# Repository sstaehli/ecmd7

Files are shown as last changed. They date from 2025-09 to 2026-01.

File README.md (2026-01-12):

# ECMD7

3-Phase Power Converter Hardware for Motor Drive Experiments.

Check the [documentation pages on gitlab.airhead.ch](https://gitlab-pages.airhead.ch/products/arnimatic/ecmd7/) or [documentation pages on GitHub](https://sstaehli.github.io/ecmd7/) for more info.

[](
https://github.com/sstaehli/ecmd7/actions/workflows/ci.yml
)

[](
https://gitlab.airhead.ch/products/arnimatic/ecmd7/-/pipelines
)

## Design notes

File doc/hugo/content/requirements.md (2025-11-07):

---
title: "Requirements"
---

# User Requirements

## 1. Overview

The drive card should provide a power stage with high qualitiy features to drive a 3-phase motor from typical car lead or RC style lithium batteries for educational and development purposes. The PCB shall provide the required frontend to an external controller at a common logic level.
The design shall be cost optimized where possible without compromising functionality under lab conditions. The PCB shall interface directly with common low to mid priced FPGA development boards and should be easily adaptible to interface with other boards. The PCB shall provide sufficent power supply to the connected controller for standalone, mobile operation.

- Drive **500W** PMSM and other synchronous **motors** from 12V–48V (lead-acid or lithium)
- Based on **TMC6200 gate driver**
- All phase current & bus voltage **sensing** in high resolution (>12-Bit, $f_s >= 2f_{PWM}$)
- Multiple **encoder** support (ABZ, BISS-C/SSI, optionally SPI)
- Interfaces with **Arty A7**, **Zybo Z7**, or optionally **Vidor 4000**

---
## 2. Power Stage

The design shall be dimensioned for high currents to continuously deliver up to 500W from down to 12V upt to 60V. PWM frequencies shall be supported at least from 4 kHz up to 25kHz. 4 quadrant operation shall be possible with battery, an onboard or external brake chopper is optional.

- **Input Voltage**: 12V–48V (up to 60V abs max)
- **Output**: 35A RMS, 50A peak
- **External MOSFETs** (N-channel, low R_DS(on))
- **Bulk capacitors** for ripple suppression
- Reverse polarity & overvoltage protection

---
## 3. Gate Driver: TMC6200

The TCM6200 shall be chosen due to its specs matching or exceeding the requiremnts of the power stage and support for current sensing.

- 3-phase gate driver with:
  - 3x or 6x PWM support
  - SPI config & diagnostics
  - Shoot-through & UV/OV protection
  - Charge pump for 100% duty cycle
- Interfaces directly with external MOSFETs
- Supports external current sensing

---
## 4. Sensing

The design shall enable PWM synchronous sampling of all three phase currents and the DC bus voltage.

- **Current**: 3-phase sensing (inline or low-side), routed to FPGA
- **Voltage**: Phase voltages + DC bus
- **Temperature**: Optional NTC or digital sensor input for MOSFET temp

---
## 5. Encoder Interface

The design shall provide at least one commonly used sensor interface.

- Supports:
  - **BiSS-C**, **SSI**
  - **ABZ incremental**
  - **SPI encoders** (e.g., AS5047)
- 12V/5V/3.3V switchable encoder supply
- Up to 12V tolerant inputs
- ESD protection & differential receivers

---
## 6. FPGA / Logic Interface

The design shall mechanically fit directly to Digilent Arty A7 or Zybo Z7 development board.

- **PMOD-compatible** I/O headers (3.3V)
- FPGA interfaces:
  - PWM (3 or 6)
  - SPI (TMC6200, encoders)
  - Encoder signals (ABZ, BiSS-C, etc.)
- Compatible with:
  - **Arty A7**
  - **Zybo Z7**
  - **Intel Vidor 4000** (via adapter)

---
## 7. Mechanical

- PCB Size: ≤ 150mm x 100mm
- Mounting holes for heatsink/enclosure
- Connectors:
  - XT60 or screw terminals (power)
  - Screw terminals for motor phases
  - Pin headers for logic & encoders

---
## 8. Deliverables
- KiCad schematic + PCB layout
- BOM

---
## Example System Overview

```mermaid
graph TD
subgraph Power Stage
Q[Gate Driver]
W[VBus ADC]
E[U/V/W Current ADC]
R[Sensor Interface]
T[3-Phase Bridge]
Q --> T
T -.-> E
end
subgraph Dev. Kit
A[PMOD X]
B[PMOD Y]
C[PMOD Z]
end
A --> Q
W --> B
E --> B
T --> M(Motor)
M -.-> X(Sensor)
X --> R
R --> C
P(Battery) --> W
P --> T
```

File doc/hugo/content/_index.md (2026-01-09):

---
title: "Overview"
---

This is the ECMD7 reference manual. The ECMD7 - Electronically Controlled Motor Driver - is a 500W, three-phase bridge for supply voltages from 10 to 60V.

Check sources on [gitlab.airhead.ch](https://gitlab.airhead.ch/products/arnimatic/ecmd7) or [GitHub](https://github.com/sstaehli/ecmd7) 

ECMD7 PCB

The drive card provides a power stage with high qualitiy features to drive a 3-phase motor from typical car lead or RC style lithium batteries for educational and development purposes. The PCB provides the required frontend to an external controller at a common logic level.
The design is cost optimized where possible without compromising functionality under lab conditions. It can directly interface  with Digilent Arty A7 and Digilent Zybo Z7. Due to 2.54 pin headers it is easily adaptible to interface with other boards. The PCB can provide sufficent power supply to the connected controller for standalone, mobile operation.

- Drive **500W** PMSM and other synchronous **motors** from 12V–48V (lead-acid or lithium)
- Based on **TMC6200 gate driver**
- All phase current & bus voltage **sensing** in high resolution (14-Bit, $f_s>=2f_{PWM}$)
- Multiple **encoder** support (ABZ, BISS-C/SSI)
- Interfaces with **Arty A7**, **Zybo Z7**

### Additional Features

- **Onboard 12V/3A supply** for connected controller boards
- **Onboard 5V/2.5A supply** for connecting controller boards
- Dedicated **SPI diagnostic bus** with 2-to-4-line decoded chip select for:
    - TMC6200 gate driver
    - MB85RS* FRAM with at least 64kByte
    - TPM122 temperature sensor close to gate driver and power stage
- **Onboard LED** for supply rails
- **Onboard LED** for drive control and state signals
- **Probe test points** for measurments
- **Assembly options** for single ended or open collector encoder inputs to acommodate single ended encoders or hall switches
- **Selectable sensor supply**
- **Selectable 3.3V I/O voltage** internal or external

ECMD7 PCB

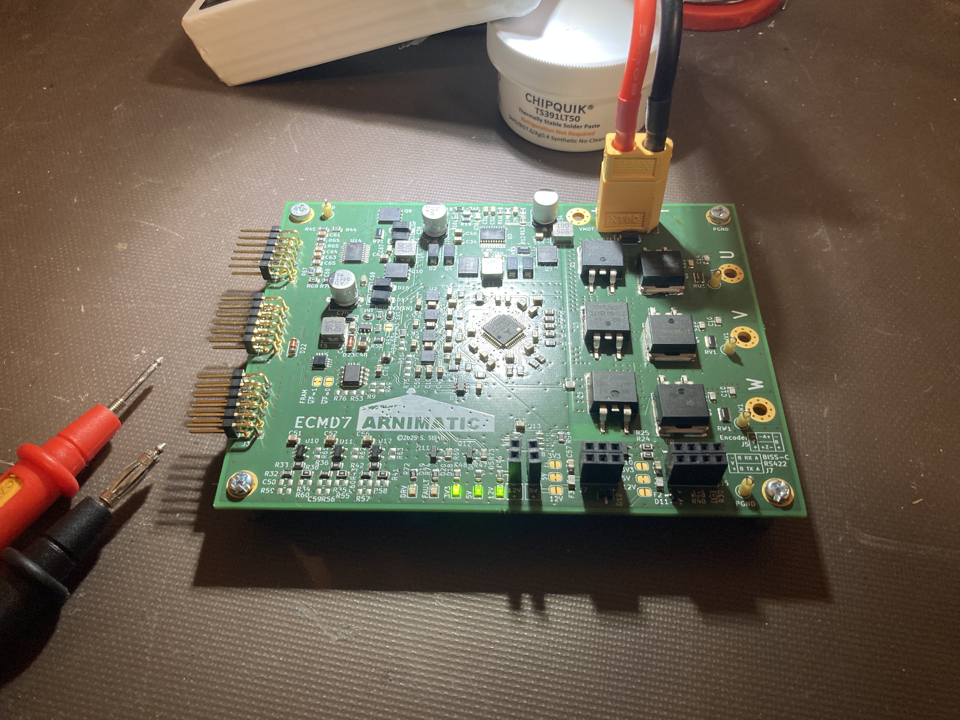
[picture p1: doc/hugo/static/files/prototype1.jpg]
ECMD7 First Prototype


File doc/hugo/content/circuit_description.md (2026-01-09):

---
title: "Circuit Description"
weight: 10
---

## Overview And PMOD Control Interface

The design mechanically fits the Digilent Arty A7 or Zybo Z7 development board.

- **PMOD-compatible** I/O headers (3.3V)
- FPGA interfaces:
  - PWM (3+3 driver signals)
  - SPI (TMC6200, encoders)
  - Encoder signals (ABZ, BiSS-C)
  - Compatible with:
    - **Arty A7**
    - **Zybo Z7**

### PMOD SPI & Encoder (J1)

| Pin # | Signal | I/O | PMOD JB (A7)*, PMOD JC (Z7)** | A7 FPGA Pin #* | Z7 SoC Pin #** | Description |
| - | - | - | - | - | - | - |
| 1 | 3.3V | In | 6 | - | - | I/O supply from FPGA board |
| 2 | 3.3V | In | 12 | - | - | I/O supply from FPGA board |
| 3 | GND | In | 5 | - | - | Signal GND |
| 4 | GND | In | 11 | - | - | Signal GND |
| 5 | ENC_B | Out | 4 | C15 | T10 | Quadrature encoder B signal |
| 6 | ENC_A | Out | 10 | J15 | U12 | Quadrature encoder A signal |
| 7 | CS1 | In | 3 | D15 | T11 | SPI Chip delect 1 for 2-to-4-line decoder |
| 8 | ENC_Z | Out | 9 | K15 | T12 | Quadrature encoder Z (Ref) signal |
| 9 | SPI_SCK | In | 2 | E16 | W15 | SPI Clock |
| 10 | CS0 | In | 8 | J18 | Y14 | SPI Chip delect 0 for 2-to-4-line decoder |
| 11 | SPI_SDI | In | 1 | E15 | V15 | SPI serial data in (from Controller) |
| 12 | SPI_SDO | Out/HiZ | 7 | J17 | W14 | SPI serial data out (to controller) |

### PMOD ADC & BiSS-C/RS422 Rx/Tx (J2)

| Pin # | Signal | I/O | PMOD JC (A7)*, PMOD JD (Z7)** | A7 FPGA Pin #* | Z7 SoC Pin #** | Description |
| - | - | - | - | - | - | - |
| 1 | 3.3V | In | 6 | - | - | I/O supply from FPGA board |
| 2 | 3.3V | In | 12 | - | - | I/O supply from FPGA board |
| 3 | GND | In | 5 | - | - | Signal GND |
| 4 | GND | In | 11 | - | - | Signal GND |
| 5 | RS422_RX | Out | 4 | V11 | R14 | RS422 receive signal (to controller) |
| 6 | RS422_TX | In | 10 | U13 | V18 | RS422 transmit signal (from controller) |
| 7 | AD_SDO_IW | Out | 3 | V10 | P14 | SPI serial data output from W-Phase current ADC |
| 8 | AD_SDO_VBUS | Out | 9 | T13 | V17 | SPI serial data output from bus voltage ADC |
| 9 | AD_SDO_IU | Out | 2 | V12 | T15 | SPI serial data output from U-Phase current ADC |
| 10 | AD_SDO_IV | Out | 8 | V14 | U15 | SPI serial data output from V-Phase current ADC |
| 11 | /CS_AD | In | 1 | U12 | T14 | SPI /CS line. Rising edge starts conversion, low level enables data output on AD_SCK rising edges |
| 12 | AD_SCK | In | 7 | U14 | W14 | SPI clock signal |

### PMOD Drive Control (J3)

| Pin # | Signal | I/O | PMOD JD (A7)*, PMOD JE (Z7)** | A7 FPGA Pin #* | Z7 SoC Pin #** | Description |
| - | - | - | - | - | - | - |
| 1 | 3.3V | In | 6 | - | - | I/O supply from FPGA board |
| 2 | 3.3V | In | 12 | - | - | I/O supply from FPGA board |
| 3 | GND | In | 5 | - | - | Signal GND |
| 4 | GND | In | 11 | - | - | Signal GND |
| 5 | DRV_EN | Out | 4 | F3 | H15 | Gate driver enable signal, active high |
| 6 | FAULT | In | 10 | G2 | Y17 | Gate driver fault signal, active high |
| 7 | WL | Out | 3 | F4 | J15 | Phase W low side switch control |
| 8 | WH | Out | 9 | H2 | T17 | Phase W high side switch control |
| 9 | VL | Out | 2 | D3 | W16 | Phase V low side switch control |
| 10 | VH | Out | 8 | D2 | U17 | Phase V high side switch control |
| 11 | UL | Out | 1 | D4 | V12 | Phase U low side switch control |
| 12 | UH | Out | 7 | E2 | V13 | Phase U high side switch control |

#### References

> *[Digilent Arty A7 Reference Manual](https://digilent.com/reference/programmable-logic/arty-a7/reference-manual)

> **[Digilent Zybo Z7 Reference Manual](https://digilent.com/reference/programmable-logic/zybo-z7/reference-manual)

---
## Power Stage

The design is dimensioned for high currents to continuously deliver up to 500W from 12V up to 60V. PWM frequencies are supported from 4 kHz up to 25kHz. 4 quadrant operation is possible with battery. There is no brake chopper.

- **Input Voltage**: 12V–48V (up to 60V abs max)
- **Output**: 35A RMS, 50A peak
- **60V/40A, low RDSOn MOSFETs** (N-channel, low R_DS(on))
- Mechanical reverse polarity protection
- Overvoltage protection

### Battery (J4) and Motor Phase Connections (U, V, W)

- A 12-48 Battery or 4-Qudrant Power Supply can be connected to the **XT60 connector J4** or the mounting holes **PGND** and **VMot**
- The Motor terminals can be connected to **M3 mounting holes U, V and W**

### Gate Driver (U1)

The [TCM6200](../files/datasheet/TMC6200_datasheet_rev1.08.pdf) matches or exceeds the requiremnts for controlling the power stage and provides support for current sensing.

- 3-phase gate driver with:
  - 3x or 6x PWM support
  - SPI config & diagnostics
  - Shoot-through & UV/OV protection
  - Charge pump for 100% duty cycle
- Interfaces directly with external MOSFETs
- Supports external current sensing

---
## ADC

The design supports PWM synchronous sampling of all three phase currents and the DC bus voltage.

- **Current**: 3-phase sensing (inline or low-side), routed to FPGA
- **Voltage**: Phase voltages + DC bus
- **Temperature**: digital sensor input for MOSFET temp

The ADC are of type [MCP3315141](../files/datasheet/MCP3315141-Data-Sheet-DS20006220.pdf)

---
## Sensors

The design provides two commonly used sensor interfaces.

- Supports:
  - **ABZ incremental**
  - **BiSS-C**, **SSI**
- 12V/5V/3.3V switchable encoder supply
- Up to 12V tolerant inputs
- differential receivers for ABZ incremental encorer
- RS422 Rx/Tx for BiSS-C
- ESD protection on all inputs

The quadrature encoder interface transforms differential signals to single ended 3.3V signals with a propagation delay of < 50 ns.

The BiSS-C/RS422 interface provides a robust, 12 Mb/s RS422 signaling from and to 3.3V IO on the controller side.

There is also a temperature sensor of type [TMP122](../files/datasheet/tmp122.pdf).

### ABZ Encoder Connector (J5)

A quadrature encoder with differential output can be connected to J5.

| Pin # | Signal |
| --- | --- |
| 1 | B- |
| 2 | B+ |
| 3 | A+ |
| 4 | Z- |
| 5 | A- |
| 6 | Z+ |
| 7 | GND |
| 8 | V_ABZ* |

*V_ABZ can by set soldering **one** jumper of JP1, JP2 or JP4.

5V is pre-connected on the PCB and has to be cut before one of the other voltages can be applied.
  
| V_ABZ | JP1 | JP2 | JP4 |
| - | - | - | - |
| 3.3V | | | x |
| 5V | | x | |
| 12V  | x | | |

**WARNING!** Soldering mutiple jumpers shorts supplies and reults in damage of the ECMD PCB.

> **NOTE:** The input circuit can be reconfigured for single ended and/or signals requiring pull-up or pull/down resistors. Consult the schematic for details.

### BiSS-C/RS-422 Connector (J7)

A BiSS-C encoder or RS-422 device can be connected to J5.

| Pin # | Signal |
| --- | --- |
| 1 | B- |
| 2 | B+ |
| 3 | A+ |
| 4 | Z- |
| 5 | A- |
| 6 | Z+ |
| 7 | GND |
| 8 | V_BISS_C* |

*V_BISS_C can by set soldering **one** jumper of JP1, JP2 or JP4.

5V is pre-connected on the PCB and has to be cut before one of the other voltages can be applied.
  
| V_BISS_C | JP5 | JP6 | JP7 |
| - | - | - | - |
| 3.3V | | | x |
| 5V | | x | |
| 12V  | x | | |

**WARNING!** Soldering mutiple jumpers shorts supplies and reults in damage of the ECMD PCB.

---
## Memory + CS Decoder

The board features an [MB85RS512](../files/MB85RS512T-DS501-00029-0v01-E.pdf) FRAM memory (U16). The memory can be used to store any kind of data, e. g. configuration or calibation. When JP10 is shorted, /WP = 1, (No write protection)
When JP12 is shorted, /WP = 0, (Write protection)

A 2-to-4 line decoder is provided to control 4 chip selects for SPI peripherals.

| CS1 | CS0 | /CS | Device |
| --- | --- | --- | --- |
| 0 | 0 | - | 
| 0 | 1 | 1 | Drive Controller U1 |
| 1 | 0 | 2 | FRAM U16 |
| 1 | 1 | 3 | Temperature Sensor U17 |

**WARNING!** Soldering both jumpers shorts the +3.3V rail and results in damage of the ECMD PCB.

---

## Power Supply

The power supplies are designed to provide sufficient power to supply also the controller board.
12V and 5V supplies are designed around a [LM5118](../files/datasheet/lm5118.pdf) IC, U13 and U14 respectively. The circuits were dimensioned with TI Vebbench.

- [12V Calculation](../files/datasheet/LM5118-12V-3A.pdf)
- [5V Calculation](../files/datasheet/LM5118-5V-2A.pdf)

The 3V supply is designed around a [LT1616](../files/datasheet/lt1616.pdf). The 3V supply can be enabled externally trough 3.3V IO (JP3 shorted, JP8 and JP5 open) or internally from 12V with 3.3V and 3.3V IO shorted.

### 12V Connector (J6)

Max. 3A

**NOTE:** This connector can be used to supply 12V to an Arty A7 on its connector J7, pins 7 (GND) and 8 (+)

### 5V Connector (J8)

Max. 2A

**NOTE:** This connector can be used to supply 5V to a Zybo Z7 on its connector its JP6, pin 2 (+) and J16.

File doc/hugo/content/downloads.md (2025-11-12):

---
title: "Downloads"
weight: 90
---

[📄 Schematic PDF](../files/schematic.pdf)

[📄 Assembly PDF](../files/assembly.pdf)

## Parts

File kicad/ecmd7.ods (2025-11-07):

Multiplier | 3 |  |  |  |  | Mouser
Qty | Totl Qty | Stock | Order | Reference | Footprint | ¨ | Value | DNP | Datasheet
1 | 3 | Alt: SMAJ33A | #VALUE! | D21 | Diode_SMD:D_SMA |  | SMAJ60A |  | https://www.littelfuse.com/media?itemid=75e32973-b177-4ee3-a0ff-cedaf1abdb93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
5 | 15 |  | 15 | D9,D10,D11,D12,D13 | Package_TO_SOT_SMD:SOT-23-3 |  | ESDA5V3L |  | https://www.st.com/resource/en/datasheet/esdal.pdf
6 | 18 | 5 | 13 | Q1,Q2,Q3,Q4,Q5,Q6 | Package_TO_SOT_SMD:TO-263-2 |  | IRFS3806 |  | https://www.infineon.com/dgdl/irfs4115pbf.pdf?fileId=5546d462533600a401535636e5d2218f
4 | 12 |  | 12 | U2,U4,U5,U7 | SSTA:TDFN10_MN_MCH |  | MCP33151-05T-E/MN |  | https://ww1.microchip.com/downloads/aemDocuments/documents/MSLD/ProductDocuments/DataSheets/MCP3315141-Data-Sheet-DS20006220.pdf
5 | 15 | 5 | 10 | R15,R71,RU1,RV1,RW1 | Resistor_SMD:R_0612_1632Metric |  | 15m |  | ~
5 | 15 | 6 | 9 | R21,R32,R38,R43,R50 | Resistor_SMD:R_0805_2012Metric |  | 820 |  | ~
3 | 9 |  | 9 | R13,R45,R67 | Resistor_SMD:R_0805_2012Metric |  | 15k |  | ~
3 | 9 |  | 9 | F1,F2,F3 | Fuse:Fuse_0805_2012Metric |  | Polyfuse |  | ~
3 | 9 |  | 9 | C44,C45,C46 | Capacitor_SMD:C_0805_2012Metric |  | 2.2n |  | ~
4 | 12 | 3 | 9 | C34,C40,C68,C69 | Capacitor_SMD:C_0805_2012Metric |  | 470n |  | ~
6 | 18 | 9 | 9 | C13,C14,C15,C16,C17,C18 | Capacitor_SMD:C_0805_2012Metric |  | 1n |  | ~
4 | 12 | 4 | 8 | L1,L2,L5,L6 | Inductor_SMD:L_TechFuse_SL0530 |  | 10u |  | ~
2 | 6 |  | 6 | R14,R66 | Resistor_SMD:R_0805_2012Metric |  | 18k |  | ~
4 | 12 | 6 | 6 | Q7,Q8,Q9,Q10 | Package_TO_SOT_SMD:TDSON-8-1 |  | BSC098N10NS5 |  | http://www.infineon.com/dgdl/Infineon-BSC098N10NS5-DS-v02_00-EN.pdf?fileId=5546d4624ad04ef9014ae95ab4221bfd
2 | 6 |  | 6 | C39,C70 | Capacitor_SMD:CP_Elec_6.3x9.9 |  | 330u |  | ~
2 | 6 | 3 | 3 | U3,U14 | Package_SO:Texas_PWP0020A |  | LM5118MH |  | https://www.ti.com/lit/ds/symlink/lm5118.pdf
1 | 3 |  | 3 | U17 | SSTA:DBV6 |  | TMP122AIDBVR |  | https://www.ti.com/lit/gpn/tmp122
1 | 3 |  | 3 | U16 | Package_SO:SOP-8_3.76x4.96mm_P1.27mm |  | MB85RS1MT |  | http://www.fujitsu.com/downloads/MICRO/fsa/pdf/products/memory/fram/MB85RS16-DS501-00014-6v0-E.pdf
1 | 3 |  | 3 | U15 | Package_SO:SSOP-8_2.95x2.8mm_P0.65mm |  | 74LVC1G139 |  | http://www.ti.com/lit/sg/scyt129e/scyt129e.pdf
1 | 3 |  | 3 | U6 | Package_TO_SOT_SMD:SOT-23-5 |  | TLV71318PDBV |  | http://www.ti.com/lit/ds/symlink/tlv713p.pdf
3 | 9 | 6 | 3 | R55,R58,R60 | Resistor_SMD:R_0805_2012Metric |  | 820 | DNP | ~
1 | 3 |  | 3 | R70 | Resistor_SMD:R_0805_2012Metric |  | 3k |  | ~
1 | 3 |  | 3 | R54 | Resistor_SMD:R_0805_2012Metric |  | 120 |  | ~
1 | 3 |  | 3 | R52 | Resistor_SMD:R_0805_2012Metric |  | 16k |  | ~
1 | 3 |  | 3 | R37 | Resistor_SMD:R_0805_2012Metric |  | 7.5k |  | ~
1 | 3 |  | 3 | R19 | Resistor_SMD:R_0805_2012Metric |  | 36k |  | ~
1 | 3 |  | 3 | L3 | Inductor_SMD:L_0805_2012Metric |  | 10u |  | ~
1 | 3 |  | 3 | J8 | Connector_PinSocket_2.54mm:PinSocket_1x02_P2.54mm_Vertical |  | 5V |  | ~
1 | 3 |  | 3 | J7 | Connector_PinHeader_2.54mm:PinHeader_2x03_P2.54mm_Vertical |  | RS422/BISS-C |  | ~
1 | 3 |  | 3 | J6 | Connector_PinSocket_2.54mm:PinSocket_1x02_P2.54mm_Vertical |  | 12V |  | ~
1 | 3 |  | 3 | J5 | Connector_PinHeader_2.54mm:PinHeader_2x04_P2.54mm_Vertical |  | Encoder |  | ~
1 | 3 |  | 3 | J4 | Connector_AMASS:AMASS_XT60-M_1x02_P7.20mm_Vertical |  | Conn_01x02_Socket |  | ~
1 | 3 |  | 3 | D22 | Diode_SMD:D_MiniMELF |  | BZV55B3V6 |  | https://assets.nexperia.com/documents/data-sheet/BZV55_SER.pdf
1 | 3 |  | 3 | D20 | Diode_SMD:D_0805_2012Metric |  | FAULT |  | ~
1 | 3 |  | 3 | D19 | Diode_SMD:D_0805_2012Metric |  | DRV_EN |  | ~
1 | 3 |  | 3 | D18 | Diode_SMD:D_0805_2012Metric |  | 3.3V |  | ~
1 | 3 |  | 3 | D6 | Diode_SMD:D_0805_2012Metric |  | 5V |  | ~
1 | 3 |  | 3 | D5 | Diode_SMD:D_0805_2012Metric |  | 12V |  | ~
1 | 3 |  | 3 | C66 | Capacitor_SMD:C_0805_2012Metric |  | 220p |  | ~
1 | 3 |  | 3 | C36 | Capacitor_SMD:C_0805_2012Metric |  | 100p |  | ~
1 | 3 |  | 3 | C35 | Capacitor_SMD:C_0805_2012Metric |  | 8.2n |  | ~
1 | 3 |  | 3 | C24 | Capacitor_SMD:C_0805_2012Metric |  | 2.2u/25V |  | ~
1 | 3 |  | 3 | C23 | Capacitor_SMD:C_0805_2012Metric |  | 4.7u/25V |  | ~
1 | 3 | 2 | 1 | U13 | Package_SO:SOIC-8_3.9x4.9mm_P1.27mm |  | ADM3490ExR |  | https://www.analog.com/media/en/technical-documentation/data-sheets/ADM3483E_3486E_3488E_3490E_3491E.pdf
1 | 3 | 3 | 0 | J3 | Connector_PinHeader_2.54mm:PinHeader_2x06_P2.54mm_Horizontal |  | PMOD_DRV |  | ~
1 | 3 | 3 | 0 | J2 | Connector_PinHeader_2.54mm:PinHeader_2x06_P2.54mm_Horizontal |  | PMOD_ADC_MPIO |  | ~
1 | 3 | 3 | 0 | J1 | Connector_PinHeader_2.54mm:PinHeader_2x06_P2.54mm_Horizontal |  | PMOD_SPI_ENC |  | ~
5 | 15 | OK | 0 | C26,C27,C28,C37,C48 | Capacitor_SMD:C_0805_2012Metric |  | 1u/25V |  | ~
3 | 9 | 10 | 0 | U10,U11,U12 | Package_TO_SOT_SMD:SOT-23-5 |  | FIN1002M5X |  | https://www.onsemi.com/pub/Collateral/FIN1002-D.pdf
1 | 3 | 4 | 0 | U9 | Package_TO_SOT_SMD:SOT-23-6 |  | LT1616ES6#TRPBF |  | https://www.analog.com/media/en/technical-documentation/data-sheets/lt1616fs.pdf
1 | 3 | 3 | 0 | U1 | SSTA:eTQFP48_9x9_TRI |  | TMC6200-TA |  | https://www.analog.com/media/en/technical-documentation/data-sheets/TMC6200_datasheet_rev1.08.pdf
1 | 3 | OK | 0 | TPW1 | TestPoint:TestPoint_Loop_D2.50mm_Drill1.0mm |  | W |  | ~
1 | 3 | OK | 0 | TPV1 | TestPoint:TestPoint_Loop_D2.50mm_Drill1.0mm |  | V |  | ~
1 | 3 | OK | 0 | TPU1 | TestPoint:TestPoint_Loop_D2.50mm_Drill1.0mm |  | U |  | ~
1 | 3 | OK | 0 | TP2 | TestPoint:TestPoint_Loop_D2.50mm_Drill1.0mm |  | PGND |  | ~
1 | 3 | OK | 0 | TP1 | TestPoint:TestPoint_Loop_D2.50mm_Drill1.0mm |  | GND |  | ~
4 | 12 | OK | 0 | R9,R49,R53,R76 | Resistor_SMD:R_0805_2012Metric |  | 4.7k | DNP | ~
3 | 9 | OK | 0 | R61,R62,R63 | Resistor_SMD:R_0805_2012Metric |  | 100k | DNP | ~
3 | 9 | OK | 0 | R56,R57,R59 | Resistor_SMD:R_0805_2012Metric |  | 1.8k | DNP | ~
6 | 18 | OK | 0 | R5,R8,R10,R26,R27,R28 | Resistor_SMD:R_0805_2012Metric |  | 10 |  | ~
3 | 9 | OK | 0 | R46,R69,R73 | Resistor_SMD:R_0805_2012Metric |  | 4.7k |  | ~
3 | 9 | OK | 0 | R34,R35,R41 | Resistor_SMD:R_0805_2012Metric |  | 1.8k |  | ~
7 | 21 | OK | 0 | R16,R48,R33,R36,R42,R72,R74 | Resistor_SMD:R_0805_2012Metric |  | 330 |  | ~
2 | 6 | OK | 0 | R31,R75 | Resistor_SMD:R_0805_2012Metric |  | 4.7k | DNP | ~
6 | 18 | OK | 0 | R22,R23,R24,R25,R39,R40 | Resistor_SMD:R_0805_2012Metric |  | 3.9k |  | ~
3 | 9 | OK | 0 | R20,R51,R64 | Resistor_SMD:R_0805_2012Metric |  | 10k |  | ~
2 | 6 | OK | 0 | R18,R68 | Resistor_SMD:R_0805_2012Metric |  | 1k |  | ~
2 | 6 | OK | 0 | R12,R44 | Resistor_SMD:R_0805_2012Metric |  | 68k |  | ~
2 | 6 | OK | 0 | R11,R65 | Resistor_SMD:R_0805_2012Metric |  | 1M |  | ~
6 | 18 | OK | 0 | R1,R2,R3,R4,R6,R7 | Resistor_SMD:R_0805_2012Metric |  | 0.1 |  | ~
1 | 3 | OK | 0 | R47 | Resistor_SMD:R_0805_2012Metric |  | 1.5k |  | ~
1 | 3 | OK | 0 | R30 | Resistor_SMD:R_0805_2012Metric |  | 0 | DNP | ~
1 | 3 | OK | 0 | R29 | Resistor_SMD:R_0805_2012Metric |  | 0 |  | ~
1 | 3 | OK | 0 | R17 | Resistor_SMD:R_0805_2012Metric |  | 8.2k |  | ~
2 | 6 | OK | 0 | Q11,Q12 | Package_TO_SOT_SMD:SOT-23 |  | MMBT3904 |  | https://www.onsemi.com/pdf/datasheet/pzt3904-d.pdf
1 | 3 | OK | 0 | JW1 | MountingHole:MountingHole_3.2mm_M3_Pad_Via |  | Phase W |  | ~
1 | 3 | OK | 0 | JV1 | MountingHole:MountingHole_3.2mm_M3_Pad_Via |  | Phase V |  | ~
1 | 3 | OK | 0 | JU1 | MountingHole:MountingHole_3.2mm_M3_Pad_Via |  | Phase U |  | ~
8 | 24 | OK | 0 | D1,D2,D3,D4,D14,D15,D16,D17 | Diode_SMD:D_SMA |  | SK220ATR |  | ~
1 | 3 | 3 | 0 | D23 | Diode_SMD:D_MiniMELF |  | LL4148 |  | http://www.vishay.com/docs/85557/ll4148.pdf
1 | 3 | OK | 0 | D7 | Diode_SMD:D_SOD-123 |  | MBR0530 |  | http://www.mccsemi.com/up_pdf/MBR0520~MBR0580(SOD123).pdf
3 | 9 | OK | 0 | C58,C59,C60 | Capacitor_SMD:C_0805_2012Metric |  | 100n | DNP | ~
37 | 111 | OK | 0 | C1,C2,C3,C4,C5,C6,C7,C8,C9,C10,C11,C19,C20,C22,C25,C29,C30,C31,C32,C33,C38,C41,C42,C43,C47,C50,C51,C52,C55,C56,C57,C61,C62,C63,C64,C67,C76 | Capacitor_SMD:C_0805_2012Metric |  | 100n |  | ~
1 | 3 | 6 | 0 | C65 | Capacitor_SMD:C_0805_2012Metric |  | 6.8n |  | ~
1 | 3 | OK | 0 | C54 | Capacitor_SMD:CP_Elec_6.3x9.9 |  | 22u |  | ~
1 | 3 | 6 | 0 | C53 | Capacitor_SMD:C_0805_2012Metric |  | 10n |  | ~
1 | 3 | OK | 0 | C49 | Capacitor_SMD:C_0603_1608Metric |  | 100n |  | ~
1 | 3 | 9 | 0 | C21 | Capacitor_SMD:C_0805_2012Metric |  | 22n |  | ~

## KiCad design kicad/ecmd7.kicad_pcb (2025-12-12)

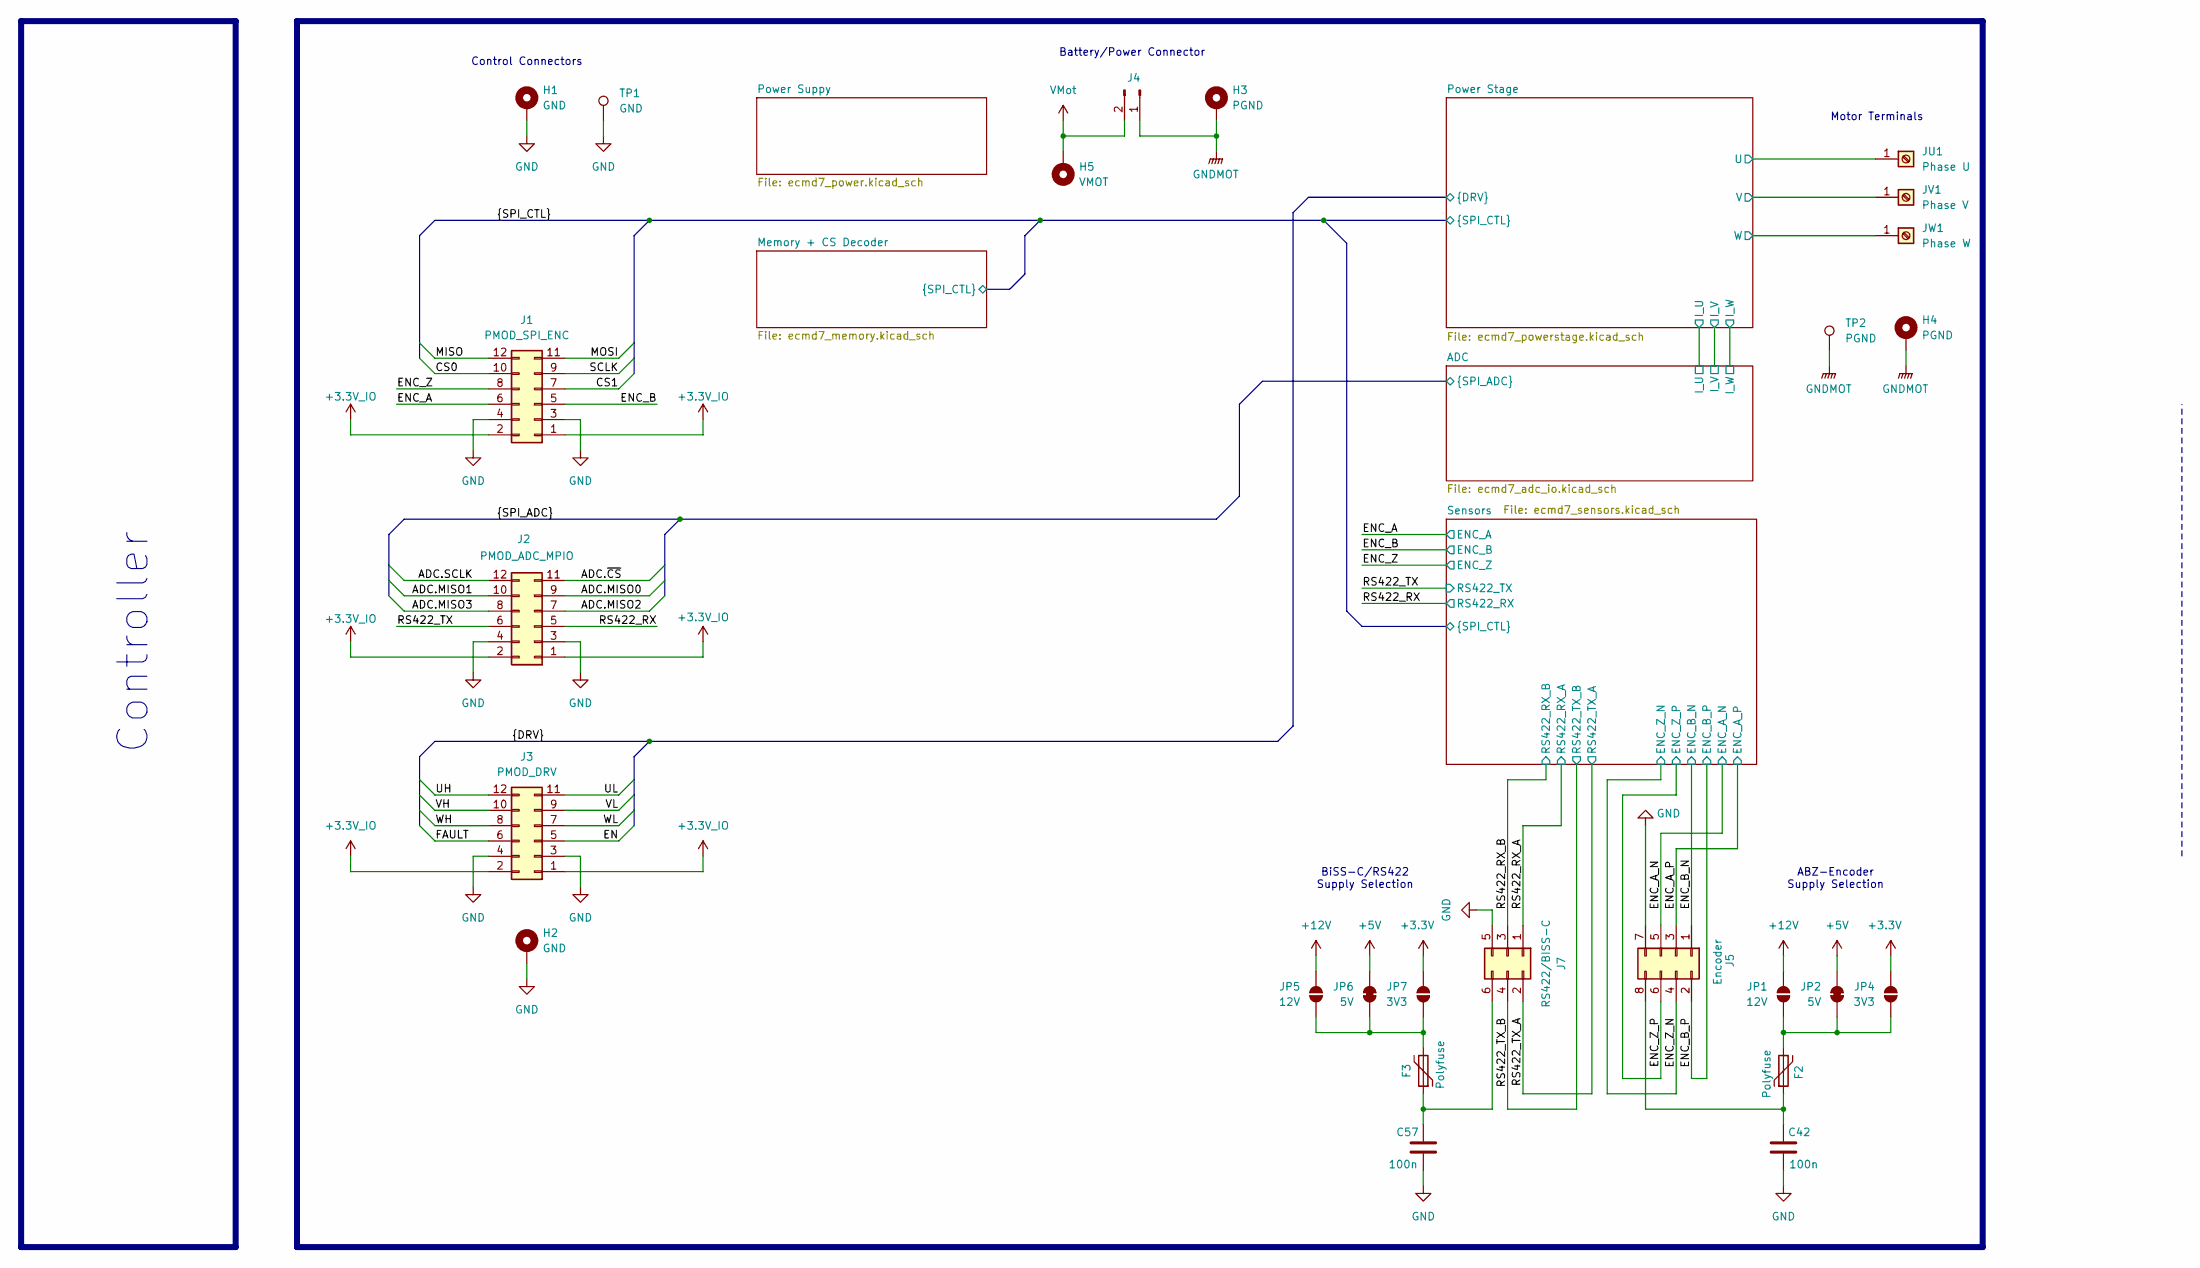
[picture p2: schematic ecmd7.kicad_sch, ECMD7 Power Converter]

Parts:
C42, C57: 100n; C_0805_2012Metric
F2, F3: Polyfuse; Fuse_0805_2012Metric
H1, H2: GND; MountingHole_3.2mm_M3_Pad_Via
H3, H4: PGND; MountingHole_3.2mm_M3_Pad_Via
H5: VMOT; MountingHole_3.2mm_M3_Pad_Via
J1: PMOD_SPI_ENC; PinHeader_2x06_P2.54mm_Horizontal
J2: PMOD_ADC_MPIO; PinHeader_2x06_P2.54mm_Horizontal
J3: PMOD_DRV; PinHeader_2x06_P2.54mm_Horizontal
J4: Conn_01x02_Socket; AMASS_XT60-M_1x02_P7.20mm_Vertical
J5: Encoder; PinHeader_2x04_P2.54mm_Vertical
J7: RS422/BISS-C; PinHeader_2x03_P2.54mm_Vertical
JP1, JP5: 12V; SolderJumper-2_P1.3mm_Open_RoundedPad1.0x1.5mm
JP2, JP6: 5V; SolderJumper-2_P1.3mm_Bridged_RoundedPad1.0x1.5mm
JP4, JP7: 3V3; SolderJumper-2_P1.3mm_Open_RoundedPad1.0x1.5mm
JU1: Phase U; MountingHole_3.2mm_M3_Pad_Via
JV1: Phase V; MountingHole_3.2mm_M3_Pad_Via
JW1: Phase W; MountingHole_3.2mm_M3_Pad_Via
TP1: GND; TestPoint_Loop_D2.50mm_Drill1.0mm
TP2: PGND; TestPoint_Loop_D2.50mm_Drill1.0mm

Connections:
+3.3V: JP4.2 (B), JP7.2 (B); also elsewhere on the board
+3.3V_IO: J1.1, J1.2, J2.1, J2.2, J3.1, J3.2; also elsewhere on the board
+5V: JP2.2 (B), JP6.2 (B); also elsewhere on the board
+12V: JP1.2 (B), JP5.2 (B); also elsewhere on the board
/ADC.MISO0: J2.9; also elsewhere on the board
/ADC.MISO1: J2.10; also elsewhere on the board
/ADC.MISO2: J2.7; also elsewhere on the board
/ADC.MISO3: J2.8; also elsewhere on the board
/ADC.SCLK: J2.12; also elsewhere on the board
/ADC.~CS: J2.11; also elsewhere on the board
/CS0: J1.10; also elsewhere on the board
/CS1: J1.7; also elsewhere on the board
/EN: J3.5; also elsewhere on the board
/ENC_A: J1.6; also elsewhere on the board
/ENC_A_N: J5.5; also elsewhere on the board
/ENC_A_P: J5.3; also elsewhere on the board
/ENC_B: J1.5; also elsewhere on the board
/ENC_B_N: J5.1; also elsewhere on the board
/ENC_B_P: J5.2; also elsewhere on the board
/ENC_Z: J1.8; also elsewhere on the board
/ENC_Z_N: J5.4; also elsewhere on the board
/ENC_Z_P: J5.6; also elsewhere on the board
/FAULT: J3.6; also elsewhere on the board
/MISO: J1.12; also elsewhere on the board
/MOSI: J1.11; also elsewhere on the board
/Power Stage/U: JU1.1; also elsewhere on the board
/Power Stage/V: JV1.1; also elsewhere on the board
/Power Stage/W: JW1.1; also elsewhere on the board
/RS422_RX: J2.5; also elsewhere on the board
/RS422_RX_A: J7.1; also elsewhere on the board
/RS422_RX_B: J7.3; also elsewhere on the board
/RS422_TX: J2.6; also elsewhere on the board
/RS422_TX_A: J7.2; also elsewhere on the board
/RS422_TX_B: J7.4; also elsewhere on the board
/SCLK: J1.9; also elsewhere on the board
/UH: J3.12; also elsewhere on the board
/UL: J3.11; also elsewhere on the board
/VH: J3.10; also elsewhere on the board
/VL: J3.9; also elsewhere on the board
/WH: J3.8; also elsewhere on the board
/WL: J3.7; also elsewhere on the board
GND: C42.2, C57.2, H1.1, H2.1, J1.3, J1.4, J2.3, J2.4, J3.3, J3.4, J5.7, J7.5, TP1.1; also elsewhere on the board
GNDMOT: H3.1, H4.1, J4.1, TP2.1; also elsewhere on the board
unnamed: C42.1, F2.1, J5.8
unnamed: C57.1, F3.1, J7.6
unnamed: F2.2, JP1.1 (A), JP2.1 (A), JP4.1 (A)
unnamed: F3.2, JP5.1 (A), JP6.1 (A), JP7.1 (A)
VMot: H5.1, J4.2; also elsewhere on the board

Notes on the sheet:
ABZ-Encoder Supply Selection
Controller
Battery/Power Connector
Motor Terminals
Control Connectors
BiSS-C/RS422 Supply Selection

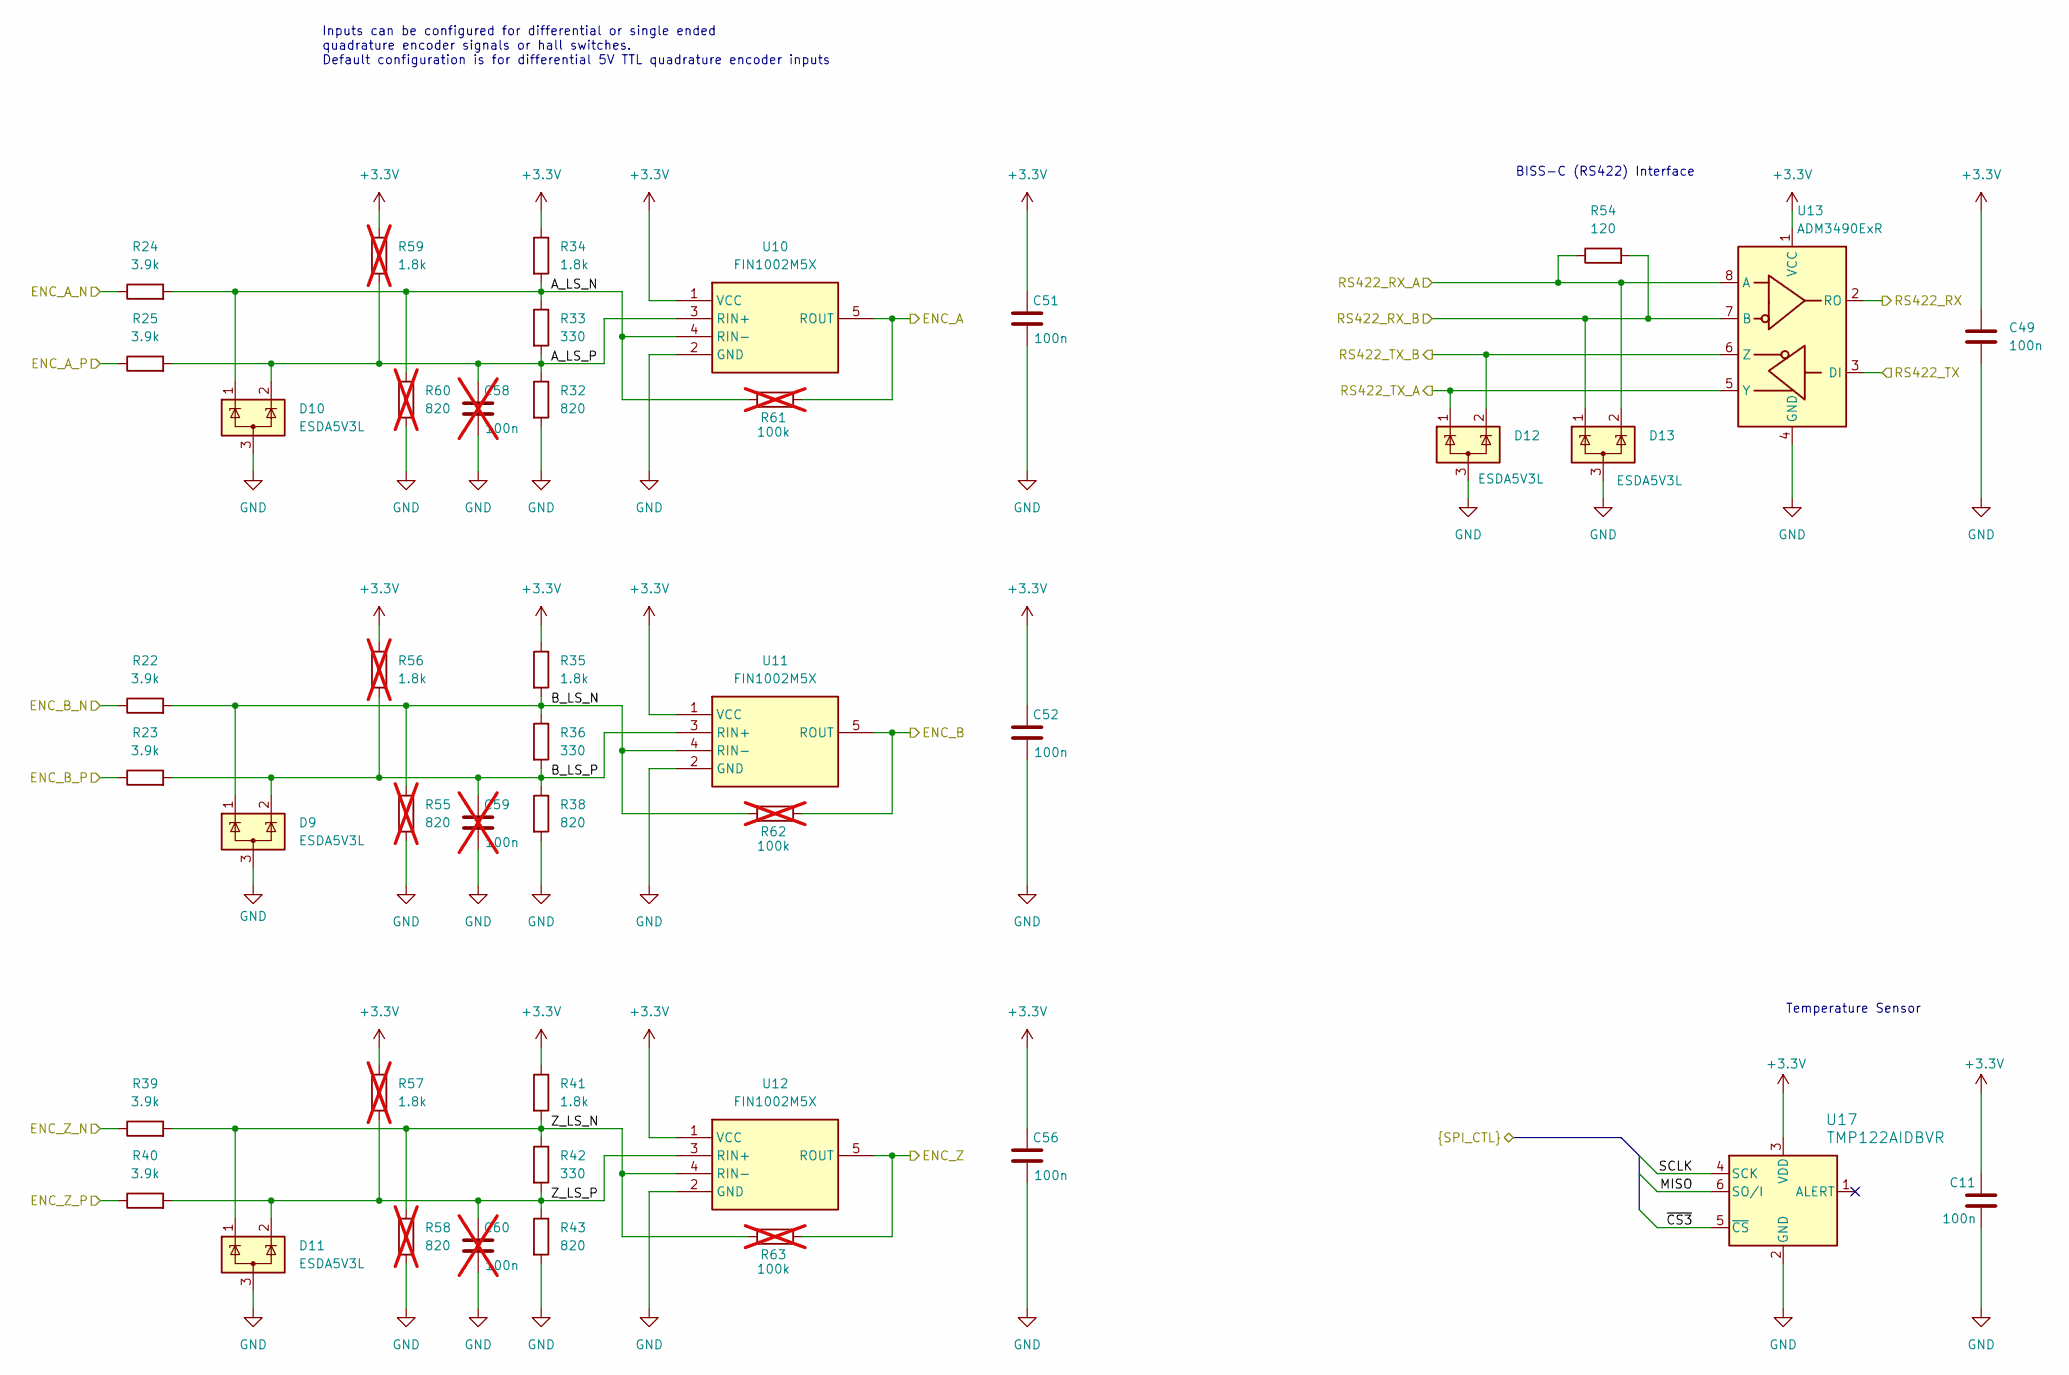
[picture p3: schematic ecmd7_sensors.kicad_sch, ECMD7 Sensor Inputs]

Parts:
C11, C51, C52, C56: 100n; C_0805_2012Metric
C49: 100n; C_0603_1608Metric; Mouser Part Number 581-06035C104KAT2A
C58, C59, C60: 100n; C_0805_2012Metric; not fitted
D9, D10, D11, D12, D13: ESDA5V3L; SOT-23-3; Mouser Part Number 511-ESDA5V3L
R22, R23, R24, R25, R39, R40: 3.9k; R_0805_2012Metric
R32, R38, R43: 820; R_0805_2012Metric
R33, R36, R42: 330; R_0805_2012Metric
R34, R35, R41: 1.8k; R_0805_2012Metric
R54: 120; R_0805_2012Metric
R55, R58, R60: 820; R_0805_2012Metric; not fitted
R56, R57, R59: 1.8k; R_0805_2012Metric; not fitted
R61, R62, R63: 100k; R_0805_2012Metric; not fitted
U10, U11, U12: FIN1002M5X; SOT-23-5; Mouser Part Number 512-FIN1002M5X
U13: ADM3490ExR; SOIC-8_3.9x4.9mm_P1.27mm; Mouser Part Number 584-ADM3490EARZ
U17: TMP122AIDBVR; DBV6

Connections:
+3.3V: C11.1, C49.1, C51.1, C52.1, C56.1, R34.1, R35.1, R41.1, R56.1, R57.1, R59.1, U10.1 (VCC), U11.1 (VCC), U12.1 (VCC), U13.1 (VCC), U17.3 (VDD); also elsewhere on the board
/ENC_A: R61.2, U10.5 (ROUT); also elsewhere on the board
/ENC_A_N: R24.1; also elsewhere on the board
/ENC_A_P: R25.1; also elsewhere on the board
/ENC_B: R62.2, U11.5 (ROUT); also elsewhere on the board
/ENC_B_N: R22.1; also elsewhere on the board
/ENC_B_P: R23.1; also elsewhere on the board
/ENC_Z: R63.2, U12.5 (ROUT); also elsewhere on the board
/ENC_Z_N: R39.1; also elsewhere on the board
/ENC_Z_P: R40.1; also elsewhere on the board
/MISO: U17.6 (SO/I); also elsewhere on the board
/RS422_RX: U13.2 (RO); also elsewhere on the board
/RS422_RX_A: D13.2 (K), R54.1, U13.8 (A); also elsewhere on the board
/RS422_RX_B: D13.1 (K), R54.2, U13.7 (B); also elsewhere on the board
/RS422_TX: U13.3 (DI); also elsewhere on the board
/RS422_TX_A: D12.1 (K), U13.5 (Y); also elsewhere on the board
/RS422_TX_B: D12.2 (K), U13.6 (Z); also elsewhere on the board
/SCLK: U17.4 (SCK); also elsewhere on the board
/Sensors/A_LS_N: D10.1 (K), R24.2, R33.1, R34.2, R60.1, R61.1, U10.4 (RIN-)
/Sensors/A_LS_P: C58.1, D10.2 (K), R25.2, R32.1, R33.2, R59.2, U10.3 (RIN+)
/Sensors/B_LS_N: D9.1 (K), R22.2, R35.2, R36.1, R55.1, R62.1, U11.4 (RIN-)
/Sensors/B_LS_P: C59.1, D9.2 (K), R23.2, R36.2, R38.1, R56.2, U11.3 (RIN+)
/Sensors/Z_LS_N: D11.1 (K), R39.2, R41.2, R42.1, R58.1, R63.1, U12.4 (RIN-)
/Sensors/Z_LS_P: C60.1, D11.2 (K), R40.2, R42.2, R43.1, R57.2, U12.3 (RIN+)
/~CS3: U17.5 (~CS); also elsewhere on the board
GND: C11.2, C49.2, C51.2, C52.2, C56.2, C58.2, C59.2, C60.2, D9.3 (A), D10.3 (A), D11.3 (A), D12.3 (A), D13.3 (A), R32.2, R38.2, R43.2, R55.2, R58.2, R60.2, U10.2 (GND), U11.2 (GND), U12.2 (GND), U13.4 (GND), U17.2 (GND); also elsewhere on the board

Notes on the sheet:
Temperature Sensor
Inputs can be configured for differential or single ended quadrature encoder signals or hall switches. Default configuration is for differential 5V TTL quadrature encoder inputs
BISS-C (RS422) Interface

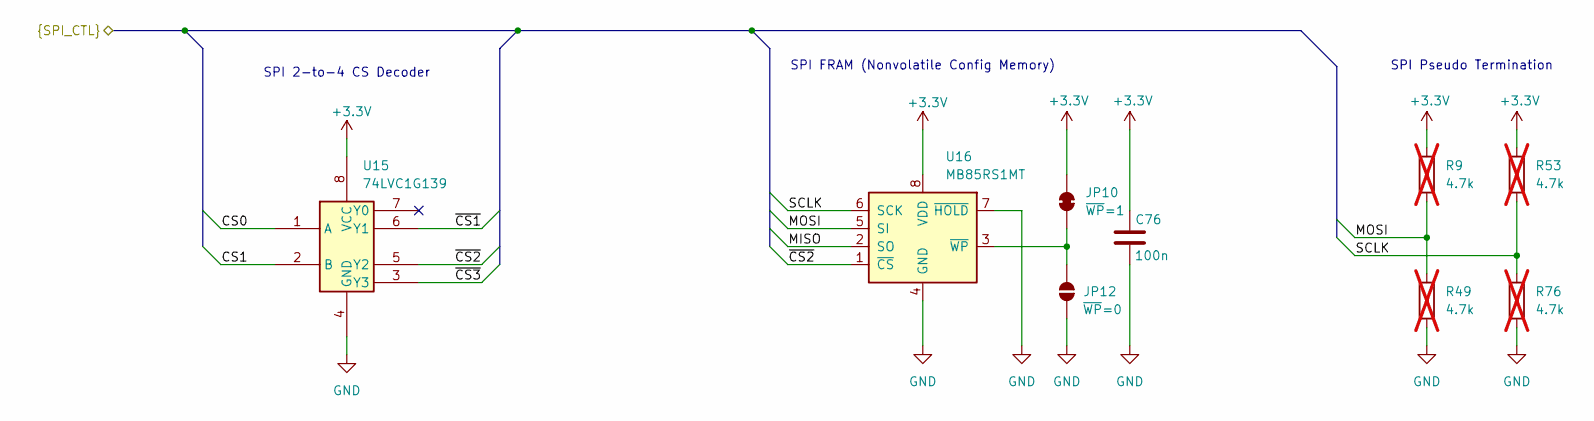
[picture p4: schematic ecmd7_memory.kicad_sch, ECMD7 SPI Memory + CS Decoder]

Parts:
C76: 100n; C_0805_2012Metric
JP10: ~{WP}=1; SolderJumper-2_P1.3mm_Bridged_RoundedPad1.0x1.5mm
JP12: ~{WP}=0; SolderJumper-2_P1.3mm_Open_RoundedPad1.0x1.5mm
R9, R49, R53, R76: 4.7k; R_0805_2012Metric; not fitted
U15: 74LVC1G139; SSOP-8_2.95x2.8mm_P0.65mm
U16: MB85RS1MT; SOP-8_3.76x4.96mm_P1.27mm

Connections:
+3.3V: C76.1, JP10.2 (B), R9.1, R53.1, U15.8 (VCC), U16.8 (VDD); also elsewhere on the board
/CS0: U15.1 (A); also elsewhere on the board
/CS1: U15.2 (B); also elsewhere on the board
/MISO: U16.2 (SO); also elsewhere on the board
/MOSI: R9.2, R49.1, U16.5 (SI); also elsewhere on the board
/SCLK: R53.2, R76.1, U16.6 (SCK); also elsewhere on the board
/~CS1: U15.6 (Y1); also elsewhere on the board
/~CS2: U15.5 (Y2), U16.1 (~CS)
/~CS3: U15.3 (Y3); also elsewhere on the board
GND: C76.2, JP12.1 (A), R49.2, R76.2, U15.4 (GND), U16.4 (GND), U16.7 (~HOLD); also elsewhere on the board
unnamed: JP10.1 (A), JP12.2 (B), U16.3 (~WP)

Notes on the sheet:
SPI 2-to-4 CS Decoder
SPI Pseudo Termination
SPI FRAM (Nonvolatile Config Memory)

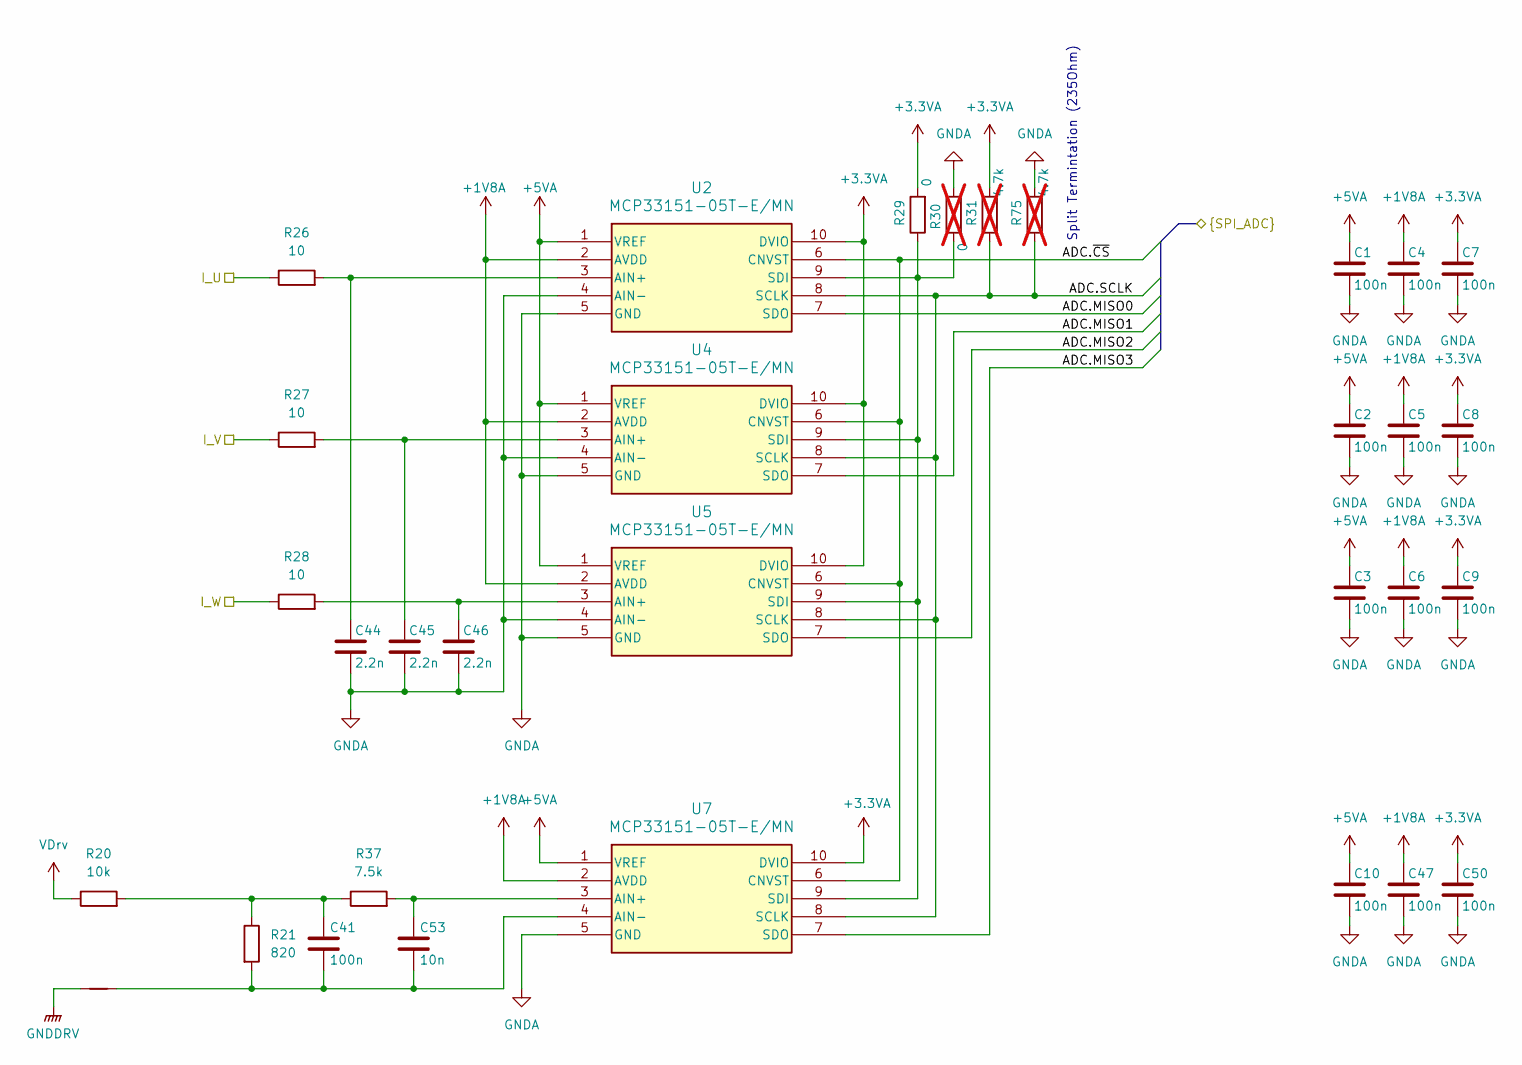
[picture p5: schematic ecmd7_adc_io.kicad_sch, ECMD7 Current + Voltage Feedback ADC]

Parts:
C1, C2, C3, C4, C5, C6, C7, C8, C9, C10, C41, C47, C50: 100n; C_0805_2012Metric
C44, C45, C46: 2.2n; C_0805_2012Metric
C53: 10n; C_0805_2012Metric
NTP2G3: NetTie_2; NetTie-2_SMD_Pad0.5mm
R20: 10k; R_0805_2012Metric
R21: 820; R_0805_2012Metric
R26, R27, R28: 10; R_0805_2012Metric
R29: 0; R_0805_2012Metric
R30: 0; R_0805_2012Metric; not fitted
R31, R75: 4.7k; R_0805_2012Metric; not fitted
R37: 7.5k; R_0805_2012Metric
U2, U4, U5, U7: MCP33151-05T-E/MN; TDFN10_MN_MCH

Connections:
+1V8A: C4.1, C5.1, C6.1, C47.1, U2.2 (AVDD), U4.2 (AVDD), U5.2 (AVDD), U7.2 (AVDD); also elsewhere on the board
+3.3VA: C7.1, C8.1, C9.1, C50.1, R29.2, R31.2, U2.10 (DVIO), U4.10 (DVIO), U5.10 (DVIO), U7.10 (DVIO); also elsewhere on the board
+5VA: C1.1, C2.1, C3.1, C10.1, U2.1 (VREF), U4.1 (VREF), U5.1 (VREF), U7.1 (VREF); also elsewhere on the board
/ADC.MISO0: U2.7 (SDO); also elsewhere on the board
/ADC.MISO1: U4.7 (SDO); also elsewhere on the board
/ADC.MISO2: U5.7 (SDO); also elsewhere on the board
/ADC.MISO3: U7.7 (SDO); also elsewhere on the board
/ADC.SCLK: R31.1, R75.1, U2.8 (SCLK), U4.8 (SCLK), U5.8 (SCLK), U7.8 (SCLK); also elsewhere on the board
/ADC.~CS: U2.6 (CNVST), U4.6 (CNVST), U5.6 (CNVST), U7.6 (CNVST); also elsewhere on the board
/ADC/I_U: R26.1; also elsewhere on the board
/ADC/I_V: R27.1; also elsewhere on the board
/ADC/I_W: R28.1; also elsewhere on the board
GNDA: C1.2, C2.2, C3.2, C4.2, C5.2, C6.2, C7.2, C8.2, C9.2, C10.2, C44.2, C45.2, C46.2, C47.2, C50.2, R30.1, R75.2, U2.4 (AIN-), U2.5 (GND), U4.4 (AIN-), U4.5 (GND), U5.4 (AIN-), U5.5 (GND), U7.5 (GND); also elsewhere on the board
GNDDRV: NTP2G3.2; also elsewhere on the board
unnamed: C41.1, R20.2, R21.1, R37.1
unnamed: C44.1, R26.2, U2.3 (AIN+)
unnamed: R29.1, R30.2, U2.9 (SDI), U4.9 (SDI), U5.9 (SDI), U7.9 (SDI)
unnamed: C45.1, R27.2, U4.3 (AIN+)
unnamed: C46.1, R28.2, U5.3 (AIN+)
unnamed: C53.1, R37.2, U7.3 (AIN+)
unnamed: C41.2, C53.2, NTP2G3.1, R21.2, U7.4 (AIN-)
VDrv: R20.1; also elsewhere on the board

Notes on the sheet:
Split Termintation (235Ohm)

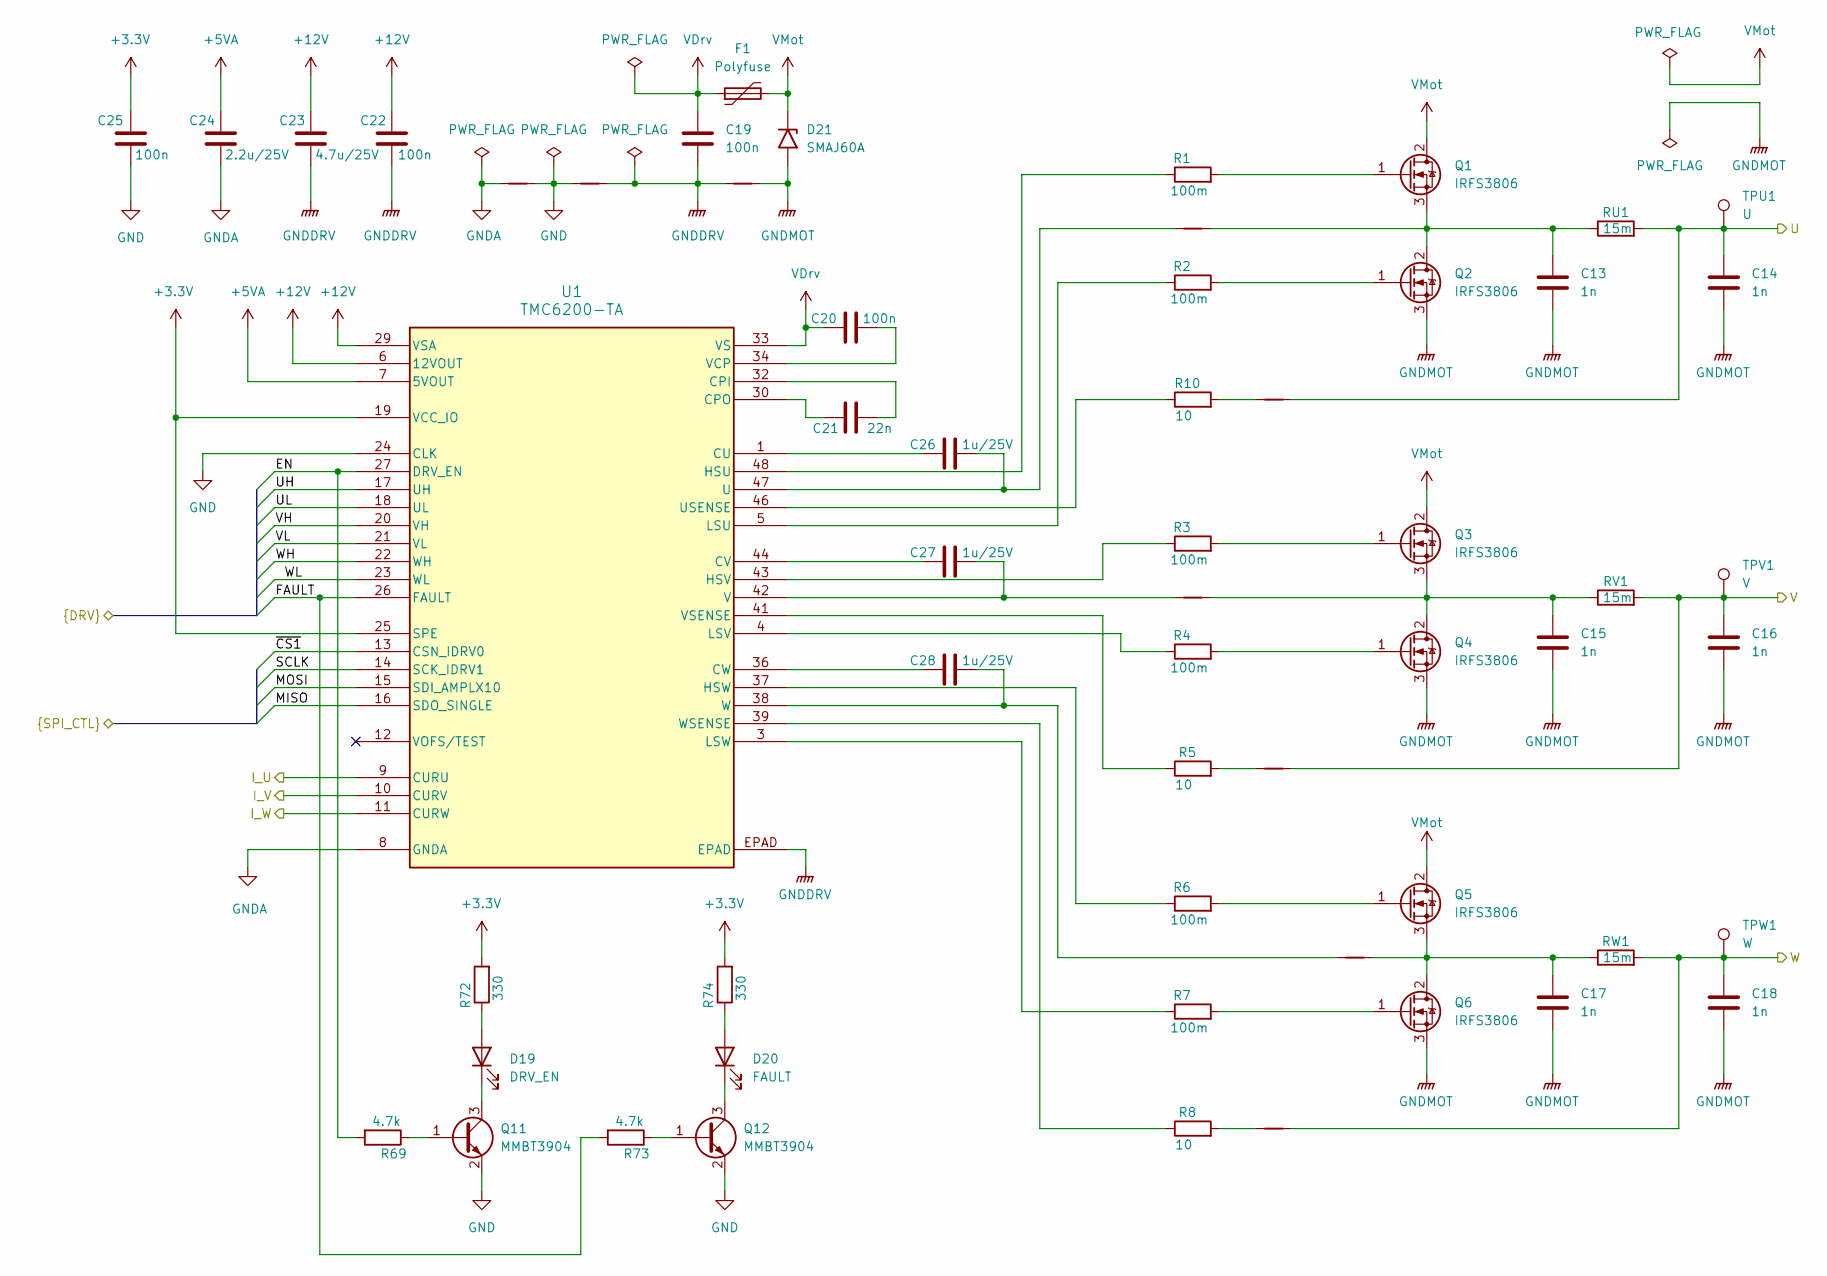
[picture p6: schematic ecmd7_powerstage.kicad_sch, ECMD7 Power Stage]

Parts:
C13, C14, C15, C16, C17, C18: 1n; C_0805_2012Metric
C19, C20, C22, C25: 100n; C_0805_2012Metric
C21: 22n; C_0805_2012Metric
C23: 4.7u/25V; C_0805_2012Metric
C24: 2.2u/25V; C_0805_2012Metric
C26, C27, C28: 1u/25V; C_0805_2012Metric
D19: DRV_EN; D_0805_2012Metric
D20: FAULT; D_0805_2012Metric
D21: SMAJ60A; D_SMA; Mouser Part Number 576-SMAJ60A
F1: Polyfuse; Fuse_0805_2012Metric
NTP2G1, NTP2G4: NetTie_2; NetTie-2_SMD_Pad2.0mm
NTP2G2: NetTie_2; NetTie-2_SMD_Pad0.5mm
NTPU1: NetTie_2; NetTie-2_SMD_Pad0.5mm
NTPV1: NetTie_2; NetTie-2_SMD_Pad0.5mm
NTPW1: NetTie_2; NetTie-2_SMD_Pad0.5mm
NTSU1: NetTie_2; NetTie-2_SMD_Pad0.5mm
NTSV1: NetTie_2; NetTie-2_SMD_Pad0.5mm
NTSW1: NetTie_2; NetTie-2_SMD_Pad0.5mm
Q1, Q2, Q3, Q4, Q5, Q6: IRFS3806; TO-263-2
Q11, Q12: MMBT3904; SOT-23
R1, R2, R3, R4, R6, R7: 100m; R_0805_2012Metric
R5, R8, R10: 10; R_0805_2012Metric
R69, R73: 4.7k; R_0805_2012Metric
R72, R74: 330; R_0805_2012Metric
RU1: 15m; R_0612_1632Metric
RV1: 15m; R_0612_1632Metric
RW1: 15m; R_0612_1632Metric
TPU1: U; TestPoint_Loop_D2.50mm_Drill1.0mm
TPV1: V; TestPoint_Loop_D2.50mm_Drill1.0mm
TPW1: W; TestPoint_Loop_D2.50mm_Drill1.0mm
U1: TMC6200-TA; eTQFP48_9x9_TRI

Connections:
+3.3V: C25.1, R72.2, R74.2, U1.19 (VCC_IO), U1.25 (SPE); also elsewhere on the board
+5VA: C24.1, U1.7 (5VOUT); also elsewhere on the board
+12V: C22.1, C23.1, U1.6 (12VOUT), U1.29 (VSA); also elsewhere on the board
/ADC/I_U: U1.9 (CURU); also elsewhere on the board
/ADC/I_V: U1.10 (CURV); also elsewhere on the board
/ADC/I_W: U1.11 (CURW); also elsewhere on the board
/EN: R69.2, U1.27 (DRV_EN); also elsewhere on the board
/FAULT: R73.2, U1.26 (FAULT); also elsewhere on the board
/MISO: U1.16 (SDO_SINGLE); also elsewhere on the board
/MOSI: U1.15 (SDI_AMPLX10); also elsewhere on the board
/Power Stage/U: C14.1, NTSU1.1, RU1.2, TPU1.1; also elsewhere on the board
/Power Stage/V: C16.1, NTSV1.2, RV1.2, TPV1.1; also elsewhere on the board
/Power Stage/W: C18.1, NTSW1.2, RW1.2, TPW1.1; also elsewhere on the board
/SCLK: U1.14 (SCK_IDRV1); also elsewhere on the board
/UH: U1.17 (UH); also elsewhere on the board
/UL: U1.18 (UL); also elsewhere on the board
/VH: U1.20 (VH); also elsewhere on the board
/VL: U1.21 (VL); also elsewhere on the board
/WH: U1.22 (WH); also elsewhere on the board
/WL: U1.23 (WL); also elsewhere on the board
/~CS1: U1.13 (CSN_IDRV0); also elsewhere on the board
GND: C25.2, NTP2G1.2, NTP2G2.1, Q11.2 (E), Q12.2 (E), U1.24 (CLK); also elsewhere on the board
GNDA: C24.2, NTP2G2.2, U1.8 (GNDA); also elsewhere on the board
GNDDRV: C19.2, C22.2, C23.2, NTP2G1.1, NTP2G4.2, U1.EPAD; also elsewhere on the board
GNDMOT: C13.2, C14.2, C15.2, C16.2, C17.2, C18.2, D21.2 (A2), NTP2G4.1, Q2.3 (S), Q4.3 (S), Q6.3 (S); also elsewhere on the board
unnamed: D19.2 (A), R72.1
unnamed: D19.1 (K), Q11.3 (C)
unnamed: D20.2 (A), R74.1
unnamed: D20.1 (K), Q12.3 (C)
unnamed: NTSU1.2, R10.2
unnamed: NTSV1.1, R5.2
unnamed: NTSW1.1, R8.2
unnamed: Q1.1 (G), R1.2
unnamed: C13.1, NTPU1.1, Q1.3 (S), Q2.2 (D), RU1.1
unnamed: Q2.1 (G), R2.2
unnamed: Q3.1 (G), R3.2
unnamed: C15.1, NTPV1.1, Q3.3 (S), Q4.2 (D), RV1.1
unnamed: Q4.1 (G), R4.2
unnamed: Q5.1 (G), R6.2
unnamed: C17.1, NTPW1.1, Q5.3 (S), Q6.2 (D), RW1.1
unnamed: Q6.1 (G), R7.2
unnamed: Q11.1 (B), R69.1
unnamed: Q12.1 (B), R73.1
unnamed: C21.1, U1.32 (CPI)
unnamed: C21.2, U1.30 (CPO)
unnamed: C26.2, U1.1 (CU)
unnamed: C27.2, U1.44 (CV)
unnamed: C28.2, U1.36 (CW)
unnamed: R1.1, U1.48 (HSU)
unnamed: R3.1, U1.43 (HSV)
unnamed: R6.1, U1.37 (HSW)
unnamed: R2.1, U1.5 (LSU)
unnamed: R4.1, U1.4 (LSV)
unnamed: R7.1, U1.3 (LSW)
unnamed: C26.1, NTPU1.2, U1.47 (U)
unnamed: R10.1, U1.46 (USENSE)
unnamed: C27.1, NTPV1.2, U1.42 (V)
unnamed: C20.1, U1.34 (VCP)
unnamed: R5.1, U1.41 (VSENSE)
unnamed: C28.1, NTPW1.2, U1.38 (W)
unnamed: R8.1, U1.39 (WSENSE)
VDrv: C19.1, C20.2, F1.1, U1.33 (VS); also elsewhere on the board
VMot: D21.1 (A1), F1.2, Q1.2 (D), Q3.2 (D), Q5.2 (D); also elsewhere on the board

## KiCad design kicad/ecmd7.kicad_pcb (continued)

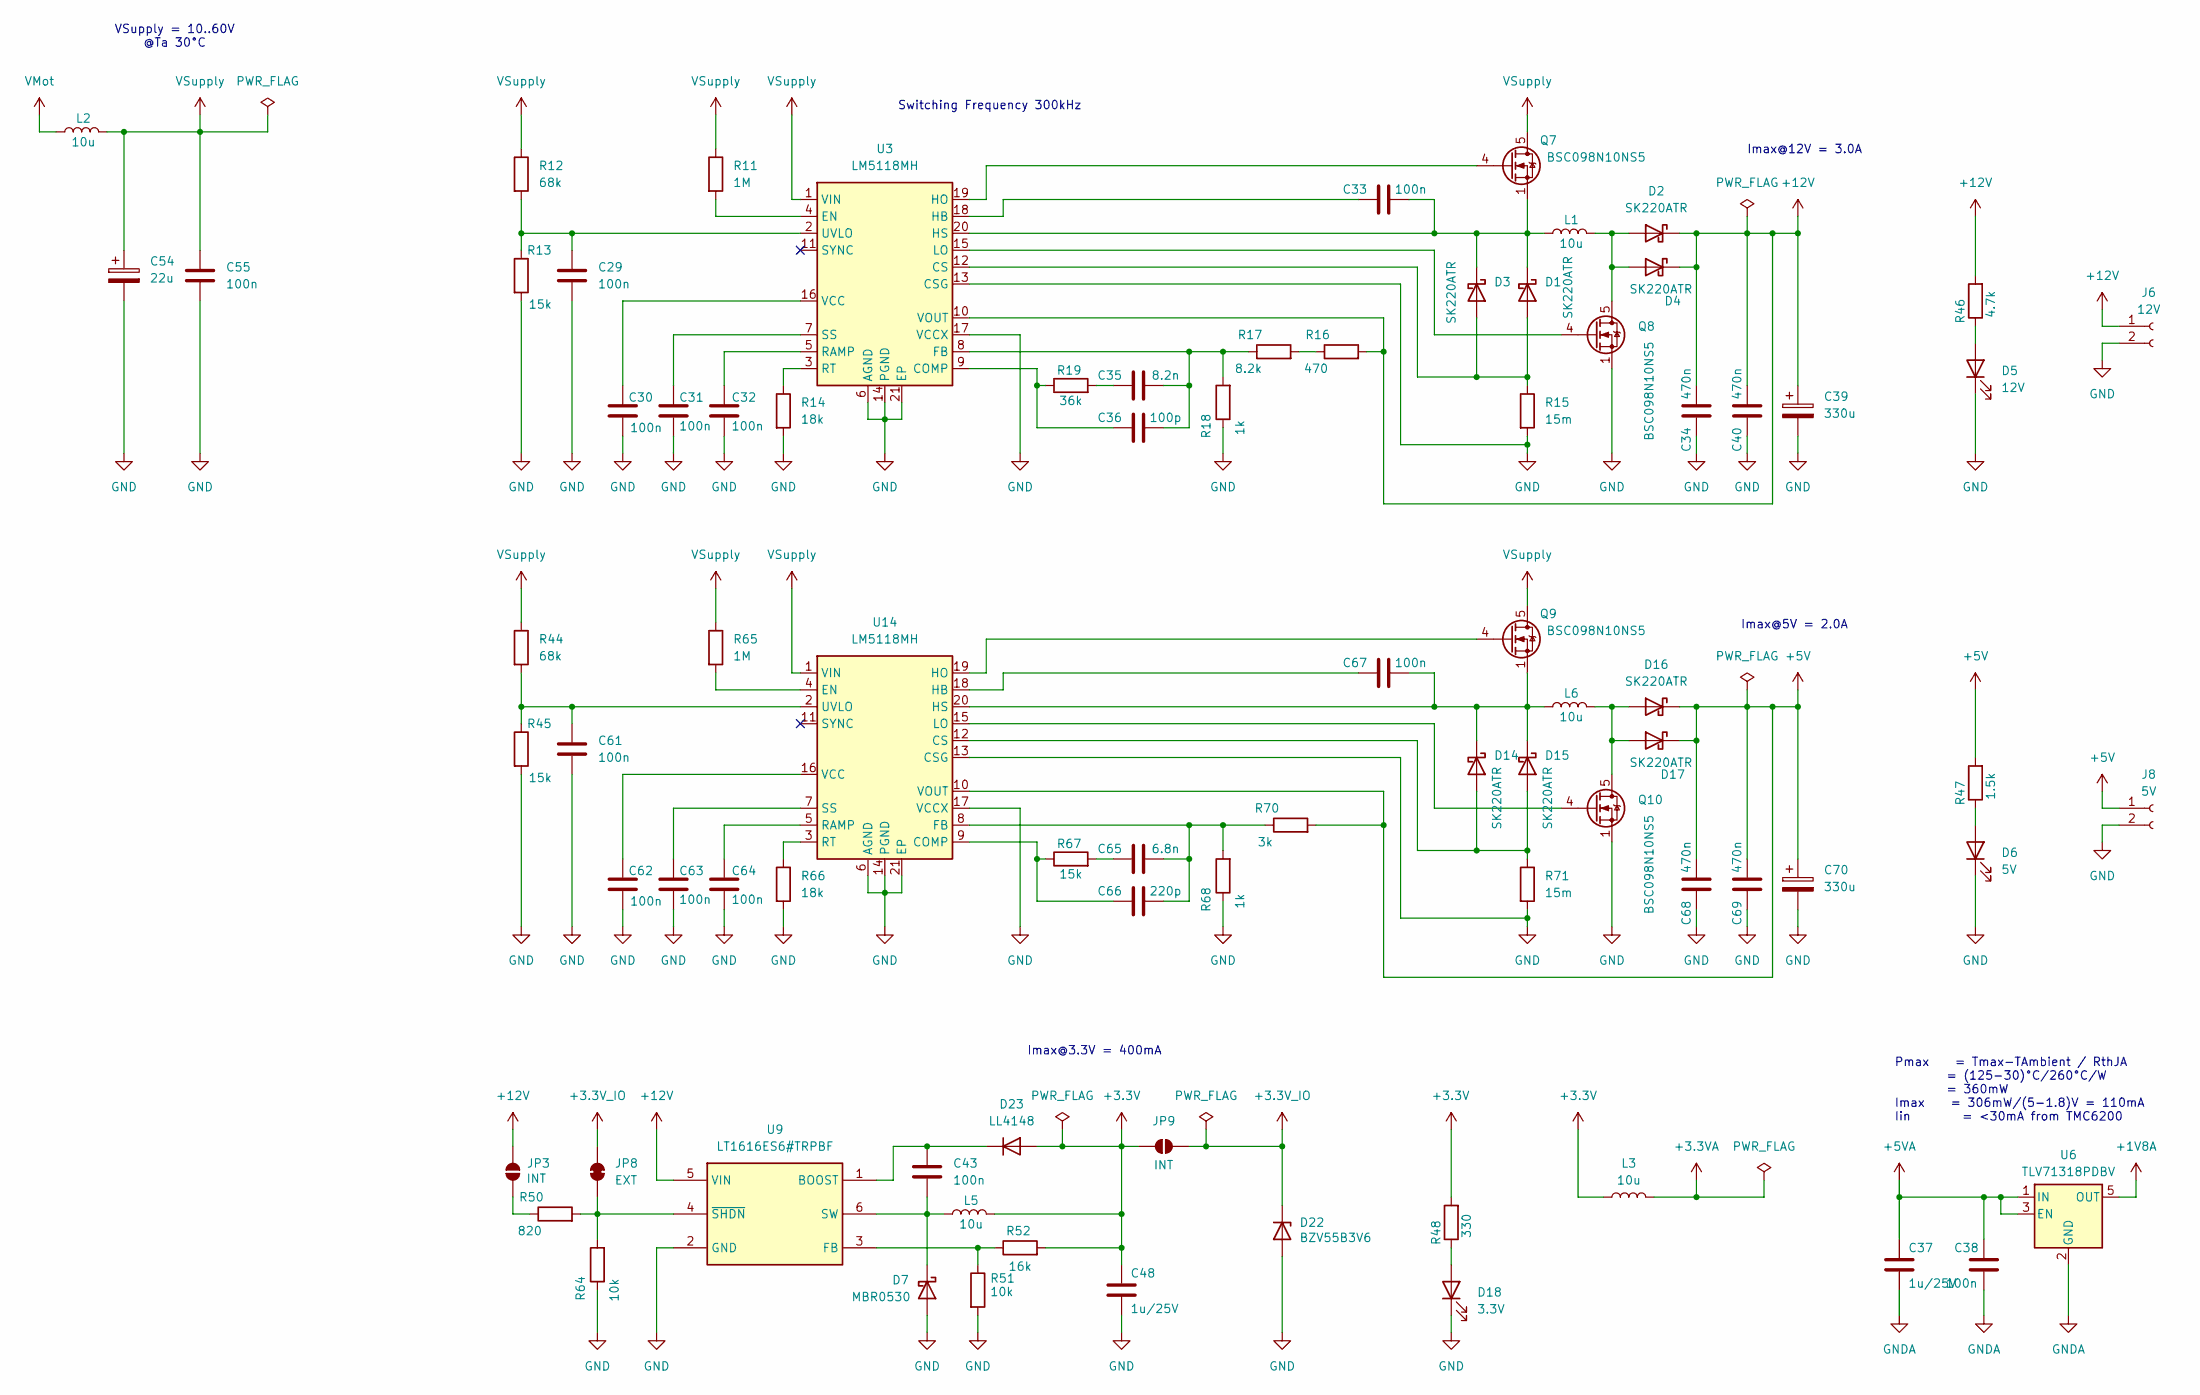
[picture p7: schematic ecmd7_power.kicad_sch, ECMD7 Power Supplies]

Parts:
C29, C30, C31, C32, C33, C38, C43, C55, C61, C62, C63, C64, C67: 100n; C_0805_2012Metric
C34, C40, C68, C69: 470n; C_0805_2012Metric
C35: 8.2n; C_0805_2012Metric
C36: 100p; C_0805_2012Metric
C37, C48: 1u/25V; C_0805_2012Metric
C39, C70: 330u; CP_Elec_6.3x9.9
C54: 22u; CP_Elec_6.3x9.9
C65: 6.8n; C_0805_2012Metric
C66: 220p; C_0805_2012Metric
D1, D2, D3, D4, D14, D15, D16, D17: SK220ATR; D_SMA
D5: 12V; D_0805_2012Metric
D6: 5V; D_0805_2012Metric
D7: MBR0530; D_SOD-123
D18: 3.3V; D_0805_2012Metric
D22: BZV55B3V6; D_MiniMELF
D23: LL4148; D_MiniMELF
J6: 12V; PinSocket_1x02_P2.54mm_Vertical
J8: 5V; PinSocket_1x02_P2.54mm_Vertical
JP3, JP9: INT; SolderJumper-2_P1.3mm_Open_RoundedPad1.0x1.5mm
JP8: EXT; SolderJumper-2_P1.3mm_Open_RoundedPad1.0x1.5mm
L1, L2, L5, L6: 10u; L_TechFuse_SL0530; Mouser Part Number 851-0530CDMCCDS100MC
L3: 10u; L_0805_2012Metric
Q7, Q8, Q9, Q10: BSC098N10NS5; TDSON-8-1
R11, R65: 1M; R_0805_2012Metric
R12, R44: 68k; R_0805_2012Metric
R13, R45, R67: 15k; R_0805_2012Metric
R14, R66: 18k; R_0805_2012Metric
R15, R71: 15m; R_0612_1632Metric
R16: 470; R_0805_2012Metric
R17: 8.2k; R_0805_2012Metric
R18, R68: 1k; R_0805_2012Metric
R19: 36k; R_0805_2012Metric
R46: 4.7k; R_0805_2012Metric
R47: 1.5k; R_0805_2012Metric
R48: 330; R_0805_2012Metric
R50: 820; R_0805_2012Metric
R51, R64: 10k; R_0805_2012Metric
R52: 16k; R_0805_2012Metric
R70: 3k; R_0805_2012Metric
U3, U14: LM5118MH; Texas_PWP0020A
U6: TLV71318PDBV; SOT-23-5
U9: LT1616ES6#TRPBF; SOT-23-6; Mouser Part Number 584-LT1616ES6#TRPBF

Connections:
+1V8A: U6.5 (OUT); also elsewhere on the board
+3.3V: C48.1, D23.2 (A), JP9.1 (A), L3.1, L5.2, R48.2, R52.2; also elsewhere on the board
+3.3VA: L3.2; also elsewhere on the board
+3.3V_IO: D22.1 (K), JP8.2 (B), JP9.2 (B); also elsewhere on the board
+5V: C68.2, C69.2, C70.1, D16.1 (K), D17.1 (K), J8.1, R47.2, R70.2, U14.10 (VOUT); also elsewhere on the board
+5VA: C37.1, C38.1, U6.1 (IN), U6.3 (EN); also elsewhere on the board
+12V: C34.2, C39.1, C40.2, D2.1 (K), D4.1 (K), J6.1, JP3.1 (A), R16.2, R46.2, U3.10 (VOUT), U9.5 (VIN); also elsewhere on the board
GND: C29.2, C30.2, C31.2, C32.2, C34.1, C39.2, C40.1, C48.2, C54.2, C55.2, C61.2, C62.2, C63.2, C64.2, C68.1, C69.1, C70.2, D5.1 (K), D6.1 (K), D7.2 (A), D18.1 (K), D22.2 (A), J6.2, J8.2, Q8.1 (S), Q8.2 (S), Q8.3 (S), Q10.1 (S), Q10.2 (S), Q10.3 (S), R13.2, R14.2, R15.2, R18.1, R45.2, R51.2, R64.1, R66.2, R68.1, R71.2, U3.6 (AGND), U3.13 (CSG), U3.14 (PGND), U3.17 (VCCX), U3.21 (EP), U9.2 (GND), U14.6 (AGND), U14.13 (CSG), U14.14 (PGND), U14.17 (VCCX), U14.21 (EP); also elsewhere on the board
GNDA: C37.2, C38.2, U6.2 (GND); also elsewhere on the board
unnamed: C35.1, R19.2
unnamed: C65.1, R67.2
unnamed: D1.2 (A), D3.2 (A), R15.1, U3.12 (CS)
unnamed: C33.2, D1.1 (K), D3.1 (K), L1.1, Q7.1 (S), Q7.2 (S), Q7.3 (S), U3.20 (HS)
unnamed: D2.2 (A), D4.2 (A), L1.2, Q8.5 (D)
unnamed: D5.2 (A), R46.1
unnamed: D6.2 (A), R47.1
unnamed: C43.2, D7.1 (K), L5.1, U9.6 (SW)
unnamed: D14.2 (A), D15.2 (A), R71.1, U14.12 (CS)
unnamed: C67.2, D14.1 (K), D15.1 (K), L6.1, Q9.1 (S), Q9.2 (S), Q9.3 (S), U14.20 (HS)
unnamed: D16.2 (A), D17.2 (A), L6.2, Q10.5 (D)
unnamed: D18.2 (A), R48.1
unnamed: C43.1, D23.1 (K), U9.1 (BOOST)
unnamed: JP3.2 (B), R50.1
unnamed: JP8.1 (A), R50.2, R64.2, U9.4 (~SHDN)
unnamed: Q7.4 (G), U3.19 (HO)
unnamed: Q8.4 (G), U3.15 (LO)
unnamed: Q9.4 (G), U14.19 (HO)
unnamed: Q10.4 (G), U14.15 (LO)
unnamed: R16.1, R17.2
unnamed: C36.1, R19.1, U3.9 (COMP)
unnamed: R11.2, U3.4 (EN)
unnamed: C35.2, C36.2, R17.1, R18.2, U3.8 (FB)
unnamed: C33.1, U3.18 (HB)
unnamed: C32.1, U3.5 (RAMP)
unnamed: R14.1, U3.3 (RT)
unnamed: C31.1, U3.7 (SS)
unnamed: C29.1, R12.2, R13.1, U3.2 (UVLO)
unnamed: C30.1, U3.16 (VCC)
unnamed: R51.1, R52.1, U9.3 (FB)
unnamed: C66.1, R67.1, U14.9 (COMP)
unnamed: R65.2, U14.4 (EN)
unnamed: C65.2, C66.2, R68.2, R70.1, U14.8 (FB)
unnamed: C67.1, U14.18 (HB)
unnamed: C64.1, U14.5 (RAMP)
unnamed: R66.1, U14.3 (RT)
unnamed: C63.1, U14.7 (SS)
unnamed: C61.1, R44.2, R45.1, U14.2 (UVLO)
unnamed: C62.1, U14.16 (VCC)
VMot: L2.1; also elsewhere on the board
VSupply: C54.1, C55.1, L2.2, Q7.5 (D), Q9.5 (D), R11.1, R12.1, R44.1, R65.1, U3.1 (VIN), U14.1 (VIN)

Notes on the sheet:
Imax@3.3V = 400mA
Imax@5V = 2.0A
Switching Frequency 300kHz
Imax@12V = 3.0A
Pmax = Tmax-TAmbient / RthJA = (125-30)°C/260°C/W = 360mW Imax = 306mW/(5-1.8)V = 110mA Iin = <30mA from TMC6200
VSupply = 10..60V @Ta 30°C

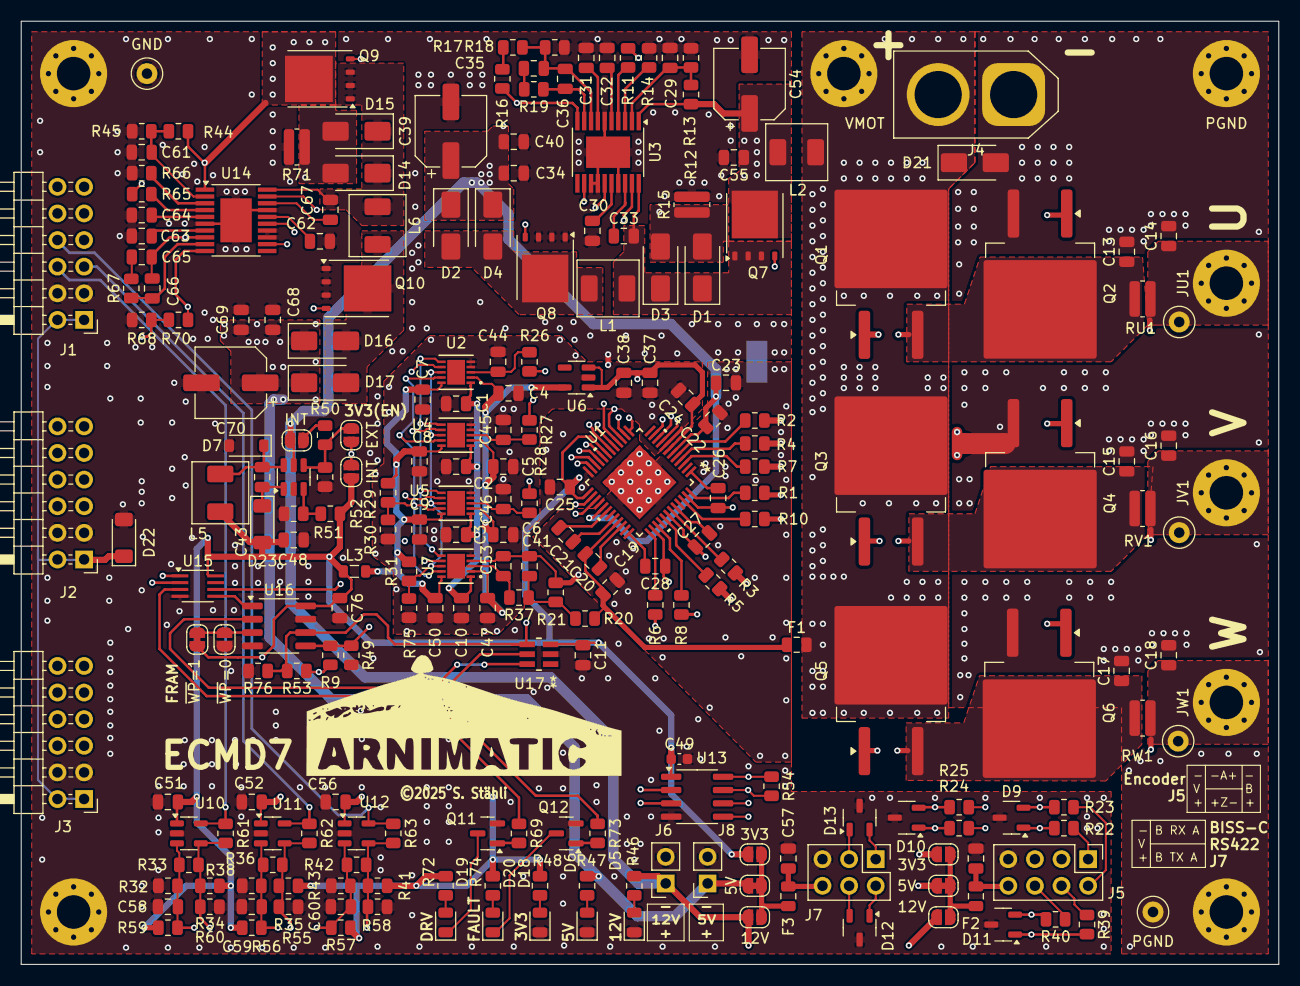
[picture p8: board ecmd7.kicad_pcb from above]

Board: 4 copper layers, 120.0 x 90.0 mm, 250 parts (1 on the bottom side), 150 nets.

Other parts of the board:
Logo: LOGO

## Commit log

2025-09-27 WIP: Add PCB
    [ADC.kicad_sch, PowerStage.kicad_sch, ecmd7.kicad_pcb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]
2025-09-27 WIP: Add supply
    [PowerStage.kicad_sch, Supply.kicad_sch, ecmd7.kicad_sch]
2025-09-27 WIP: Add ADC inputs
    [ADC.kicad_sch, PowerStage.kicad_sch, Supply.kicad_sch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]
2025-09-29 WIP: Update ADC schematic with cheaper solution
    [ADC.kicad_sch]
2025-10-01 WIP: Add sensor interface Re-partition schematic
    [Feedback.kicad_sch, Supply.kicad_sch, ecmd7.kicad_sch]
2025-10-08 Finlize schematics
    [Feedback.kicad_sch, ecmd7.kicad_sch]
2025-10-23 Finalize schematic Add ESD protection Align connector pinout with Arty A7 and Zybo Z7 PMOD
    [Feedback.kicad_sch, PowerStage.kicad_sch, ecmd7.kicad_sch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]
2025-10-23 PCB dimension and initial placement
    [ecmd7.kicad_pcb]
2025-10-24 Initial component placement
    [ecmd7.kicad_pcb, ecmd7.kicad_sch, ecmd7_adc_io.kicad_sch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]
2025-10-28 WIP: Update symbols, fix ERC errors
    [ecmd7.kicad_pcb, ecmd7.kicad_sch, ecmd7_adc_io.kicad_sch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]
2025-10-28 WIP: Power stage and ADC routing
    [ecmd7.kicad_pcb, ecmd7.kicad_sch, ecmd7_adc_io.kicad_sch]
2025-10-31 WIP: Partial routing
    [ecmd7.kicad_pcb, ecmd7.kicad_sch, ecmd7_adc_io.kicad_sch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]
2025-10-31 WIP: advnced routing
    [ecmd7.kicad_pcb, ecmd7.kicad_sch, ecmd7_adc_io.kicad_sch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]
2025-11-02 Routing complete, DRC successful
    [ecmd7.kicad_pcb, ecmd7.kicad_sch, ecmd7_adc_io.kicad_sch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]
2025-11-02 Final layout
    [ecmd7.kicad_pcb, ecmd7.kicad_sch, ecmd7_adc_io.kicad_sch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]
2025-11-02 Ordered layout
    [ecmd7.kicad_pcb]
2025-11-07 Update project structure for enhancment with firmware and software
    [ecmd7.kicad_pcb, ecmd7.kicad_sch, ecmd7.ods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]
2025-11-07 CI: Update KiCad image tag
2025-11-07 CI: Change KiCad image for 3D models
2025-11-10 Cleanup schematic
    [ecmd7.kicad_pcb, ecmd7.kicad_sch, ecmd7_adc_io.kicad_sch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]
2025-11-12 Cleanup schematic, add busses
    [ecmd7.kicad_pcb, ecmd7.kicad_sch, ecmd7_adc_io.kicad_sch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]
2025-12-10 WIP: Add power pole simulation
    [ecmd7sim.kicad_pcb, ecmd7sim.kicad_sch]
2025-12-10 General schematic cleanup
    [ecmd7.kicad_pcb, ecmd7.kicad_sch, ecmd7_adc_io.kicad_sch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]
2025-12-12 Fix MOSI/MISO naming ADC
    [ecmd7.kicad_sch, ecmd7_adc_io.kicad_sch]
2025-12-12 Fix power connector polarity
    [ecmd7.kicad_pcb, ecmd7.kicad_sch]
2026-01-08 CI: Separate Hugo build and deploy stages
2026-01-09 Update circuit description
2026-01-12 Update workflow with Gerber generation and package release
2026-01-12 Fix kicad job

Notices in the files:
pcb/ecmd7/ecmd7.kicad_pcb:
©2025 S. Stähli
